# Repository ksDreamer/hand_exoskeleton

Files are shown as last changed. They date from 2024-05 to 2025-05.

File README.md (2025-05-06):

# hand_exoskeleton 低成本机械手外骨骼

[toc]

A low-cost 6DoF hand exoskeleton using linkage and tendon mechanism under ESP32.   

一个约500元低成本6自由度的手部外骨骼，用连杆驱动四指，用线驱模拟肌腱机制驱动大拇指，主控是ESP32，动力源是七个SC09总线舵机，可以承载大于20N的负载。

开源地址：https://github.com/ksDreamer/hand_exoskeleton

视频介绍：[[开源] 500块钱的低成本6自由度手部外骨骼_灵巧手_康复手套](https://www.bilibili.com/video/BV1YzUzY8ETY/)

overview

# News 更新记录

2024-11-16: 完善README，补充细节。DIY电池座的图文攻略已完成。

2024-11-24: 上传3D打印文件，更新README。

2025-05-06: 补充拇指细节

# Getting Started 复现教程

1. 克隆仓库到本地，下载相关资源  ```git clone https://github.com/ksDreamer/hand_exoskeleton.git```

2. 修改机械结构、开始3D打印。机械结构的资源在`mechanics`文件夹里，包含SolidWorks格式模型（零件是`.SLDPRT`，总装是`_概念总装Assembly.SLDASM`，手的模型文件：`Assy 90.SLDPRT`）和FDM的3D打印文件（零件是`.stl`，总装是`_概念总装Assembly.3mf`），需要修改就自行修改（打印手的模型需缩小到原本的0.9）。

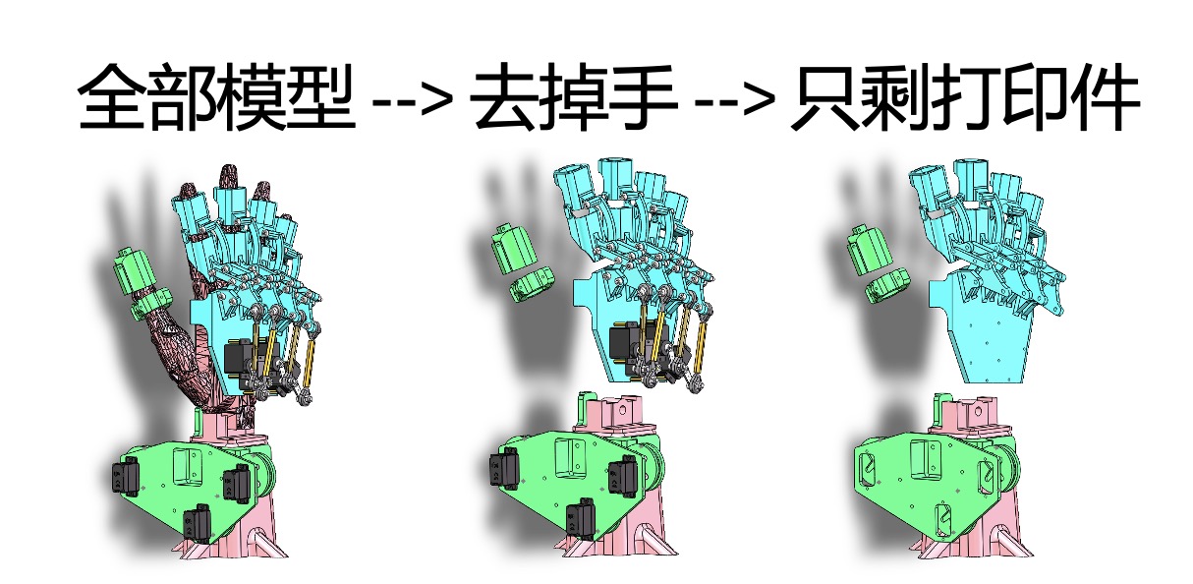
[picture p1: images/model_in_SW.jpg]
model_in_SW
   

   如图，在SOLIDWORKS里找到手的文件后点击隐藏零部件，从而只显示外骨骼。蓝色是四指部分，绿色是大拇指部分，粉色是底座。黑色是舵机，黄色是铜柱，白色是螺丝、鱼眼轴承、舵盘、舵臂。**只有蓝色、绿色和粉色的文件需要3D打印，已全部整理在`mechanics/FDM_3DPrinting`内**。经切片软件处理后3D打印。如果没接触过3D打印，欢迎阅读作者写的教程：[3D 打印机_拓竹 X1Carbon_操作指南](https://zhuanlan.zhihu.com/p/644491008)。建议3D打印时分批次，例如四指的连杆结构尽量安排临近时间打印，拇指的线驱结构也单独打印，避免零件太多混乱。

3. 组装（TODO）。四指的组装相对简单，拇指线驱有一根线要横穿过四指连杆结构的，因为要从这个方向提供拉力。

4. 电控和软件相关资源在`program`文件夹里，需要完整下载ServoDriver文件夹。

5. 配置ESP32的Arduino开发环境：跟着微雪的[Servo Driver with ESP32用户手册](https://www.waveshare.net/w/upload/d/d6/Servo-Driver-with-ESP32-user-manual-cn.pdf)操作。重要的就是选择Board：ESP32 Dev Module。选择串口（不同电脑的串口号不一定相同），注意Mac电脑的串口不叫COM，通常叫usbserial-0001

6. 连上ESP32和舵机后，用Type-C口烧录程序。保持供电。

7. 现在你可以在电脑/手机/平板等智能设备的Wi-Fi列表看到“ESP32_KevinStark"，密码是"88888888"（这些都是你可以自己设置的！），连接后就可以通过局域网访问ESP32的IP地址，从而打开Web前端控制界面了。IP地址通常是`192.168.4.1`。（ESP32支持蓝牙、Wi-Fi、ESP-NOW三种通信方式，ESP-NOW可以做机械手的示教，有空再细写相关内容教程TODO）

8. 设置舵机ID。因为买来新舵机默认ID都是1，所以需要给多个舵机分配不同的ID。通过Web界面的```ID Select+, ID Select-, ID to Set+, ID to Set-```四个按钮，或者手动烧程序来依次设置舵机ID。本项目的ID分配信息如下：大拇指从左往右1、2、3。四指从食指开始为4，小尾指为7。

9. 机械结构安装完成、电控软件准备完毕后，通常来说不能直接运行。因为每个人的安装时的机械调零、铜柱给进量等等可能不一样。建议用串口调试的方法慢慢**测试适合的角度**。

10. 开始玩耍。

# Material 材料

* 机械相关
  * SC09 总线舵机 * 7 
  * 鱼眼轴承 M3 * 8 
  * M2和M3规格的螺丝和螺母若干，六角螺丝刀，十字螺丝刀。
  * 六角铜柱 *4（内径3.2mm，长度20-38mm不定，与鱼眼轴承给进配合和软件角度配合）
  * 线 0.8mm 
  * 3D打印（本项目使用的是PLA耗材和[Bambu Studio](https://bambulab.cn/zh-cn/download/studio)切片软件）
* 电子相关
  * 主控：ESP32 微控制器 * 1 
  * 信号线和串线板（如果采用本项目列出的材料商家，会在每一份舵机包裹里配套这两个）
  * 供电：查询[微雪ESP32的文档](https://www.waveshare.net/wiki/Servo_Driver_with_ESP32)可得知ESP32板的工作电压为6\~12V，接口为5.5*2.1mm DC。查询[微雪SC09 Servo的文档](https://www.waveshare.net/wiki/SC09_Servo)得知SC09舵机的工作电压为4.8\~8.4V。因此我们需要：
    * 支持**6~12V供电**的5521 DC 口电源，因为舵机是串联总线，所以随着舵机数量增多，供电电压要相应增大。
    * 或者2节18650电池（3.7v）**串联** + 5521 DC 转接头 + 电池槽（电池座的制作教程已完成，见下图。注意细节：为了绝缘安全可以加上电工绝缘胶带、热塑管之类的，为了避免多次插拔可以接一个电源开关。但一定要注意安全！没有经验的建议上面那个选项，网购一个适合的适配器电源。）
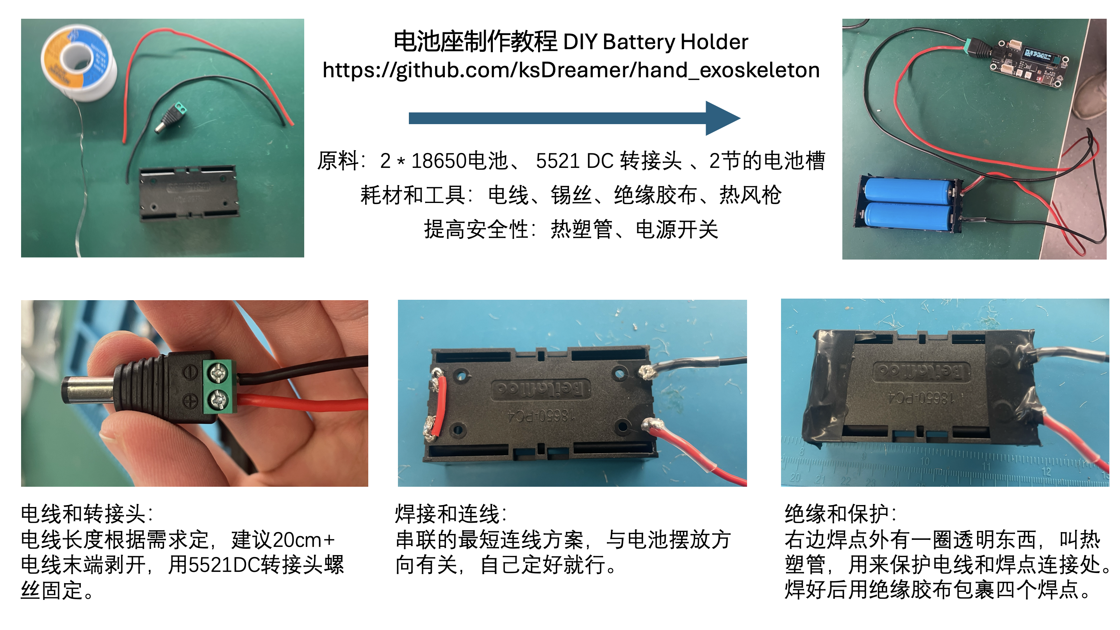
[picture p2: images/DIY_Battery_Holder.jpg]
电池座制作教程
    
  * 电线和锡丝若干
  * 电焊台
  * （可选）热风枪、热塑管、电源开关
* 软件
  * 开发：推荐VSCode开发迭代，Arduino烧录
  * 设备：支持上传程序的电脑，已在Mac和Windows上测试可行。ESP32烧录口是Type-C
  * 使用：任一能连接Wi-Fi且具有图形化窗口的设备

# Mechanics 机械介绍

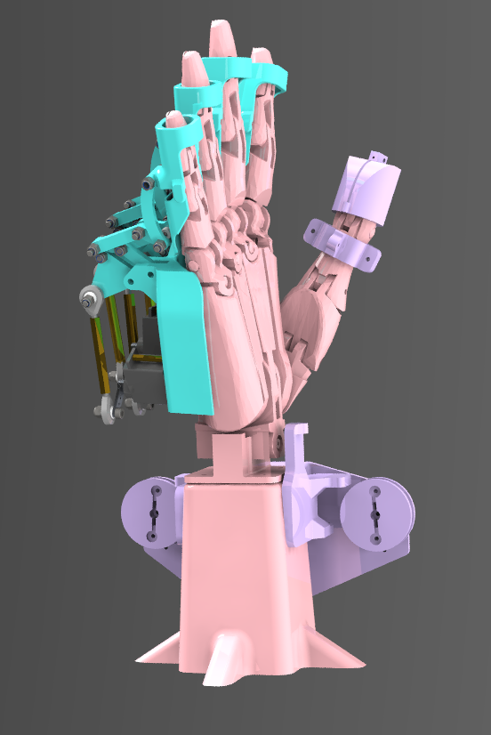
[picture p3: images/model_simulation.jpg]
model_simulation


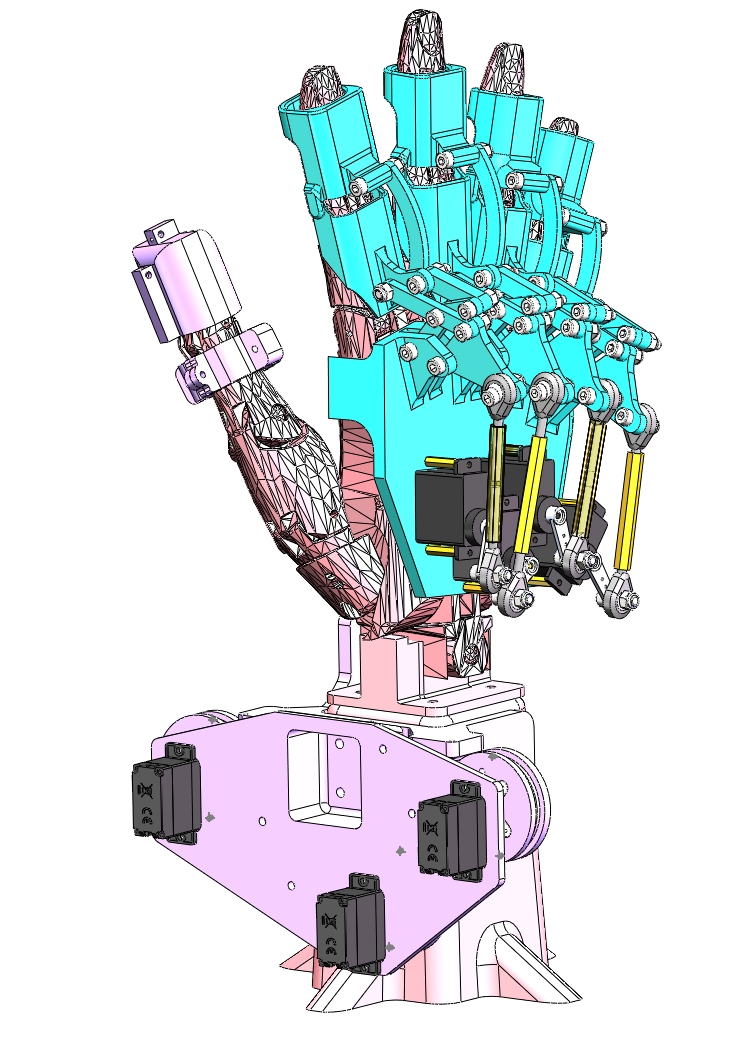
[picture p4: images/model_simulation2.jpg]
model_simulation2


## 基本信息

**连杆**与**线驱**结合控制。

重量：大拇指外骨骼174g，四指外骨骼226g，总重大约400g。（含舵机和各种零件耗材，不含手模型和电源）

尺寸：150x150x310mm

负载：四指总拉力>20N。

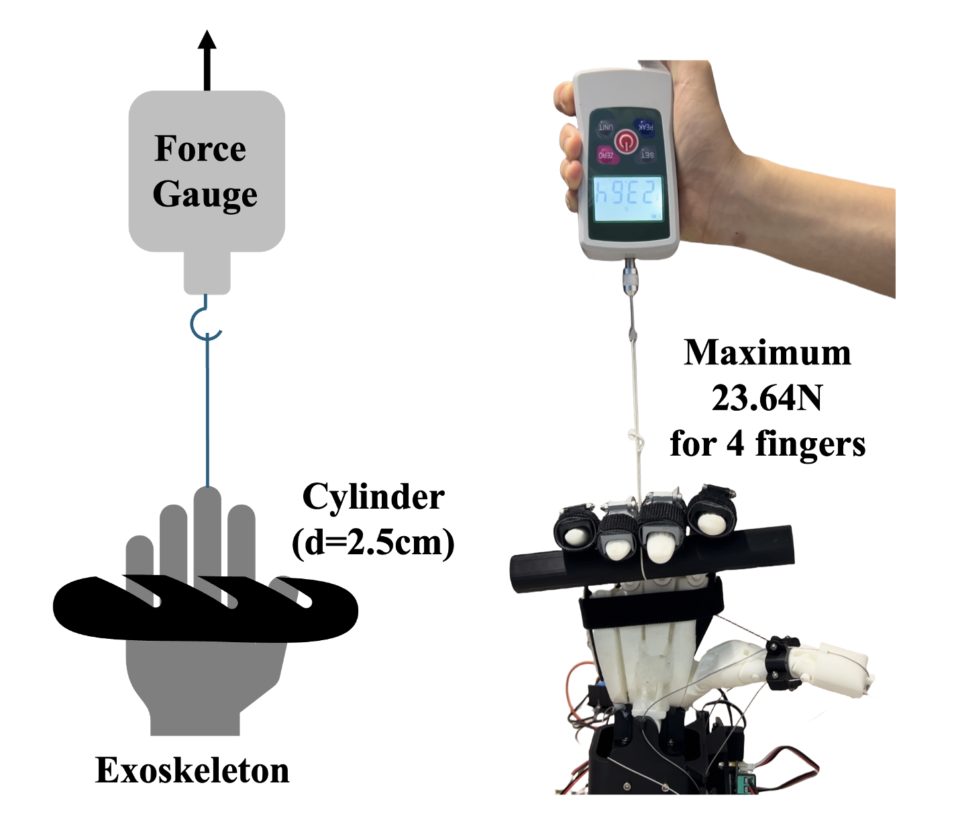
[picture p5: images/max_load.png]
max_load


与手部贴合的部分采用圆角设计，具有良好的舒适性。

四指穿戴方便，直接往手上套。大拇指需要套环和拉线，会复杂一点。

## 四指——连杆

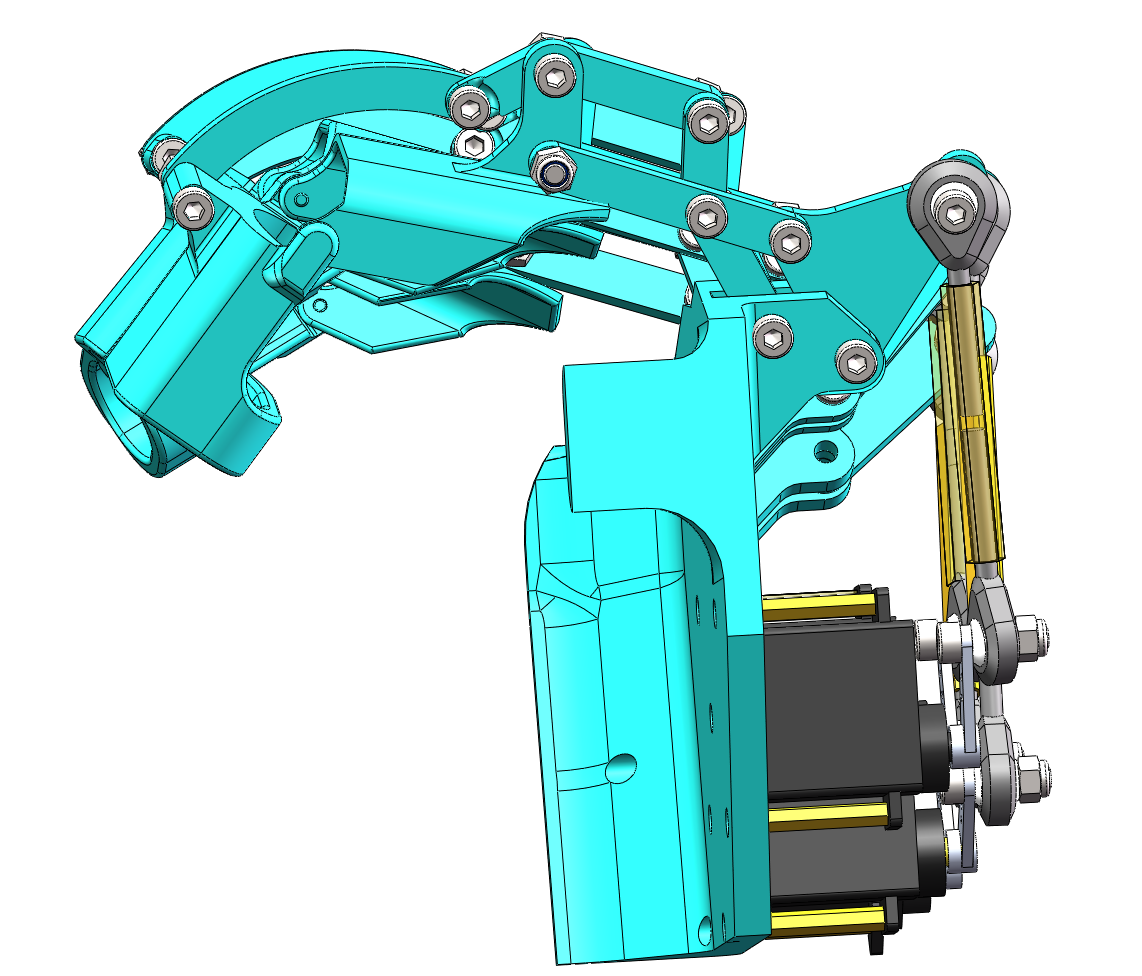
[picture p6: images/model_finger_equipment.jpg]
model_finger_equipment


传动部分通过**曲柄连杆**与**鱼眼轴承**将水平面内的运动转化为手指的竖直运动，并限制摇杆的行程，保证安全性；
执行部分每根手指采用八根连杆的系统控制，考虑到MCP关节两侧没有地方穿戴外骨骼，故通过两个平行四边形四连杆将关节引出，PIP关节通过四连杆设计方式准确控制弯曲程度，并且进一步通过螺丝之间的干涉再次保证手指不会反向弯曲。  

## 大拇指——线驱

大拇指通过三个舵机实现两自由度的紧凑灵活过驱动线驱控制。

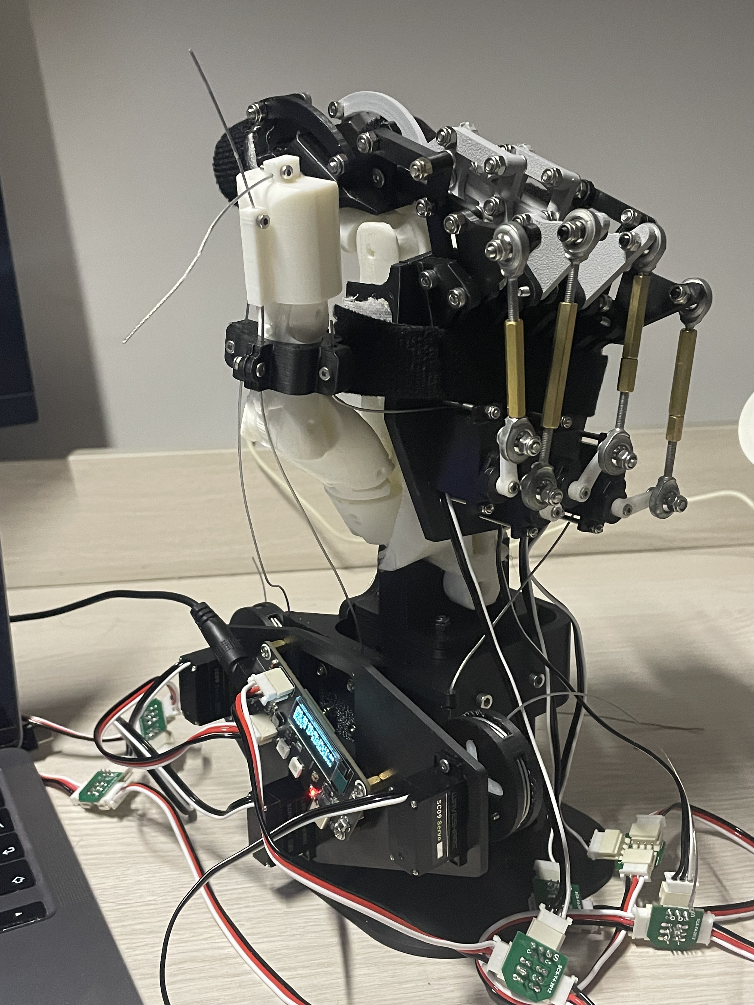
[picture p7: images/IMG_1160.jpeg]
Thumb_1

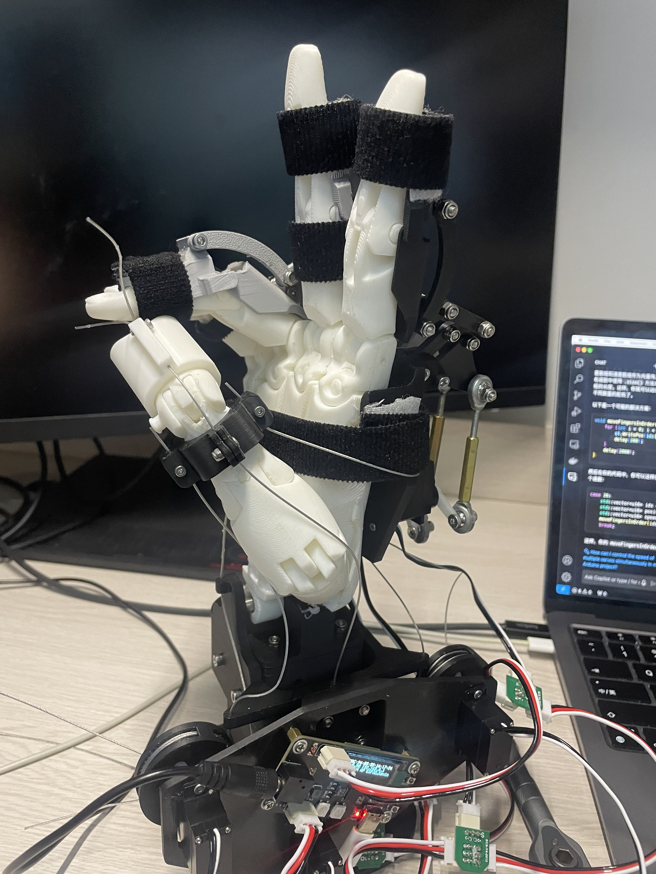
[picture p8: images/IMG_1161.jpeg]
Thumb_2

其中1号舵机和3号舵机控制一个轴的自由度，2号舵机控制水平面垂直另一个轴的自由度。

# Program 程序介绍

## 基本信息

单舵机控制：```st.WritePos(2, 450, 0,400);``` 第一项2表示舵机ID是2，第二项450表示目标角度为450，第四项400表示转动速度为400。第三项不用管。

多舵机同时控制，就把舵机ID、Position和Speed存入相应数组，```st.SyncWritePos(ID, 7, Position, 0, Speed);```分别是舵机ID，舵机数量，角度，第四项不用管，速度。

多舵机控制需要在STSCTRL.h 里定义```byte ID[]、u16 Position[]、u16 Speed[]```，方括号内填数量。

重要参考文档：

* https://www.waveshare.net/wiki/Servo_Driver_with_ESP32 

* https://www.waveshare.net/wiki/SC09_Servo

## ServoDriver.ino

ServoDriver.ino 是主程序，```void loop()```是主函数，在这里写的程序只要主控上电就会自动循环执行。

在 ```void setup()```里这几行的作用是初始化舵机，匹配舵机ID和计算机中的变量

```c++
  ID[0] = 1; //匹配舵机ID，大拇指分别为1,2,3,二到五指为4,5,6,7。有多少个就要在STSCTRL.h的byte ID[]，Position[]，Speed[]里对应修改。
  ID[1] = 2;
  ID[2] = 3;
  ID[3] = 4;
  ID[4] = 5;
  ID[5] = 6;
  ID[6] = 7;
```

只要有供电，就能在Wifi列表找到ESP32的局域网热点。连接后浏览器访问192.168.4.1可以打开web调试界面。（前提是没有把Wi-Fi相关程序注释或删除）

本程序里在```loop```里增加了串口调试的相关程序，方便开发测试。使用方法是：（设置好开发板环境、波特率等之后）Type-C连接电脑和ESP32，在Arduino右上角打开串口监视器。可以有两种输入：

* ```[ID] [Position] [Speed]```格式的单舵机转动命令，需要空格。

* ```[caseNumber]```格式的动作方案。

## CONNECT.h

在这里的```activeCtrl```里面的```switch case```添加想要的动作方案。例如case 23是写好了的```Open Hand```函数。

```c++
case 23: // Open Hand
        openHand();
        moveThumbSameTime(1000, 100, 0, setSpeed);
        break;
```

里面可以直接用前面介绍的```WritePos```等方法直接写你要的转动方案。此处的两个子函数是在外面做了函数定义和封装。查阅CONNECT.h即可查到其定义。

此处就可以做很多动作方案和软件开发相关工作了。如果感兴趣可以直接把微雪官方文件拉下来看看和本项目的有什么区别。

## WEBPAGE.h

WEBPAGE.h 是对Web前端界面的开发。本质是HTML+JavaScript+CSS。  

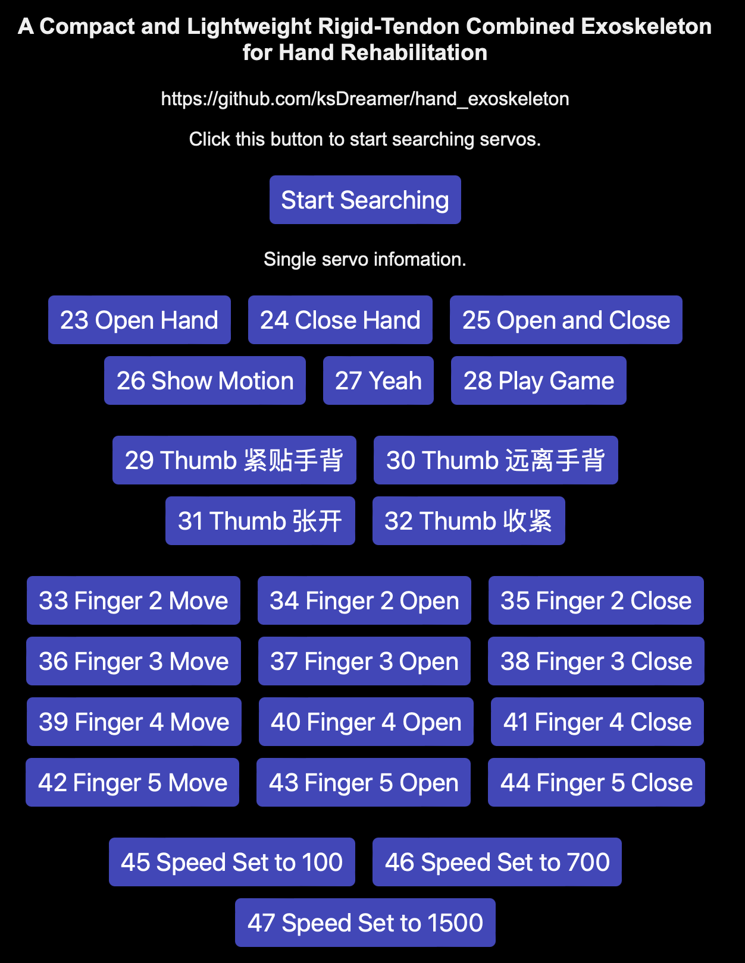
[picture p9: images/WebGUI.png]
WebGUI


要给Web前端开发新功能，想要什么动作方案就在CONNECT.h里的```active Control```函数处添加新case，然后在WEBPAGE.h里调用```toggleCheckbox```函数。（建议从case 30开始，不建议和官方的case重叠覆盖）

例如看下面这个，就是添加了一个叫做“23 Open Hand”的按钮。点击就会触发```toggleCheckbox```函数里的第二个参数对应的case。那case 23是什么呢？就需要你自己去写了，本项目case 23 对应Open Hand

```html
<label align="center"><button class="button" onclick="toggleCheckbox(1, 23, 0, 0);">23 Open Hand</button></label>
```

此处就可以做很多网页前端相关工作了。如果感兴趣可以直接把微雪官方文件拉下来看看和本项目的有什么区别。

## Developing Log 开发日志

* v0.2 测试得到四指和大拇指2号舵机的合适转动角度，放在Loop主函数里。

* v0.3 WEB前端增加四指的Move、Open、Close按钮和动作方案。根据舵臂和装置测试效果重新调整小尾指（7号舵机）转动参数以避免干涉。修改Wifi名为ESP32_KevinStark，密码为88888888。

* v0.4 增加大拇指控制方案，先```relaxThumb```让1和3号舵机的线松驰，再移动；封装了很多函数，增强可维护性；增加了很多动作方案。

* v0.5 优化代码结构，封装函数。大拇指稳定，先张开再收紧。增加动作方案例如四指和大拇指的联动，play game 石头剪刀布。整理Web前端布局。于ServoDriver.ino增加串口调试程序，可接收"[ID] [Position] [Speed]"格式的单舵机转动命令，还有"[caseNumber]"格式的动作方案。

* v1.0 增加三种Speed的选择 100 700 1500 对应case 45 46 47，只改变四指运行速度。简化前端界面。

## Cost 成本

要复现本项目，至少需要这些：

* SC09舵机 单价47元，7个，[微雪 SC09串行总线舵机300度转动角度金属齿轮舵机电机双模式切换](https://detail.tmall.com/item.htm?id=714639378997)

* ESP32开发板 单价80元，1个，[微雪 ESP32舵机驱动扩展板 wifi远程控制 蓝牙通信 支持253个舵机](https://detail.tmall.com/item.htm?id=667483395387)

* 鱼眼轴承 单价1.9元，8个，[气缸鱼眼接头关节轴承向心万向杆端球头SI内丝SA外螺纹连接杆拉杆](https://item.taobao.com/item.htm?id=725305319897)

* 线 单价2.89元，一次10米长，[304不锈钢钢丝绳 晾衣绳遮阳网包塑钢丝绳 细软小包胶钢丝绳 0.8mm](https://detail.tmall.com/item.htm?id=727898238439)

以上共需要427.09元。

电池+焊接一整套大概在30元以内，3D打印大概在30元以内（仅外骨骼最终版 不含手 不含迭代版本，按照0.2元/克PLA价格）

还有机械、电焊的耗材和工具，还有运费。

也就是说，要实现这个项目，在手头有电焊和机械工具的情况下，500元左右能搞定。

## Summary and Future Plan 总结和未来计划

本项目提供了一个低成本的6自由度手部外骨骼方案，四指部分是连杆传动，拇指是线驱。

因为成本的考虑，这个项目成品的运动精度一般，能指定角度，但无法精确。另外也没有力反馈和传感等功能。

这些在各个子领域都有相对成熟的方案了。因此做集成的难度不会很大。（但不是本项目了。舵机和连杆方案在精度和自由度的上限不高，2024-11-16留言）有条件的话，会选择更高精度的驱动方案，例如步进电机、无刷直流等等。

这个项目发展下去，想探索的一个大方向是灵巧手。

* TODO：
  * ~~DIY电池座的图文攻略（已完成）~~
  * ~~整理上传.3mf格式（已完成）~~
  * 整理上传组装细节
  * 用Web前端交互可能会出现点击一次触发3下动作的问题，暂时不清楚为何。是多个事件监视器对上一个窗口？为稳妥，推荐在问题没找到和解决前用串口控制。
* 可发展方向：
  * 主从示教（ESP-NOW通信，机械结构优化减小死区）
  * 摄像头手势识别（match case 已实现，待整理开源。精确随动还要再研究）
  * 人机交互的优化，例如语音识别输入（STT），语音喇叭模块，网页前端美化（CSS），添加用户开机引导步骤等等。
  * 力反馈和柔性接触抓握。
  * 大语言模型做动作规划（LLM+RAG）
  * 强化学习抓握训练。灵巧手抓取泛化性研究。灵巧手数据生成自监督学习研究。

## Acknowledgements 致谢

谢谢[Khlann](https://github.com/Khlann)和[cyatar](https://github.com/cyatar)在嵌入式领域提供建议。

谢谢lvWei指导焊接并分享技巧。

谢谢RobotIC机器人实验室提供了制作过程所需的部分耗材和工具。

手的模型来自助教，如知晓原出处欢迎告知。

# Reference 参考资料

1. Marcin Bonikowski, Mikulás Hajduk, Lucia Koukolova, Wojciech J. Klimasara, Patrycja Mrozek, and Zbigniew Pilat. New trends in the use of robotic devices in motor rehabilitation of upper limbs. In Automation, 2016.
2. Anirban Chowdhury, Shyam Sunder Nishad, Yogesh Kumar Meena, Ashish Dutta, and Girijesh Prasad. Hand-exoskeleton assisted progressive neurorehabilitation using impedance adaptation based challenge level adjustment method. IEEE Transactions on Haptics, 12:128–140, 2019.
3. FeiyunXiao,LiangGu,WenzhangMa,YanheZhu,ZhenZhang,andYongWang.Realtimemotion intention recognition method with limited number of surface electromyography sensors for a 7-dof hand/wrist rehabilitation exoskeleton. Mechatronics, 79:102642, 2021.
4. Phillip Tran, Seokhwan Jeong, Steven L. Wolf, and Jaydev P. Desai. Patient-specific, voice- controlled, robotic flexotendon glove-ii system for spinal cord injury. IEEE Robotics and Automation Letters, 5:898–905, 2020.
5. https://www.waveshare.net/wiki/Servo_Driver_with_ESP32 
6. https://www.waveshare.net/wiki/SC09_Servo

# Contributor 建设者

Mechanics：

CJY, [ZJR](https://github.com/peterstark1900)

Electronics：

[Kevin Stark](https://github.com/ksDreamer), [Khlann](https://github.com/Khlann)

Software:

[Kevin Stark](https://github.com/ksDreamer)

Report and other work:

ZY, LXH, [Kevin Stark](https://github.com/ksDreamer)

Thanks for reading this project. You are welcomed to make contributions to this project. If there is any problem, feel free to raise an issue. Contact me via gmy.kevinstark@gmail.com if needed.

感谢阅读本项目，欢迎复现并提出改进建议。如果有任何问题，随时可以提Issue，有需要的话可以通过 gmy.kevinstark@gmail.com 联系我。

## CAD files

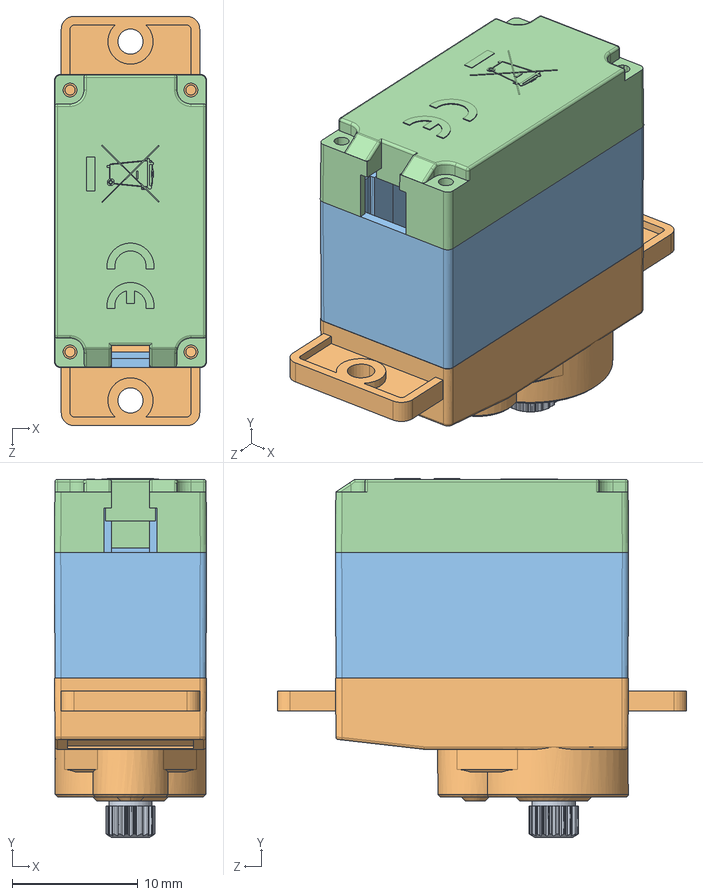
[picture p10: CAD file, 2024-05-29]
mechanics/CAD_SolidWorks/SC09-SERVO.SLDASM
12.1 x 28.5 x 32.5 mm
SJ-CL00-0027-OUTPUTGEAR-0716_37^OUTPUTGEAR_ASM_11_ASM_1_ASM_FT90M-C001_ASM_3_ASM_1_ASM_FT90M-C001-20201118_ASM_1_ASM_SC09-SERVO(2)_SC09-SERVO
SJ-WK00-0038-TOPCASE-0716_41_1^FT90M-C001_ASM_3_ASM_1_ASM_FT90M-C001-20201118_ASM_1_ASM_SC09-SERVO(2)_SC09-SERVO
SJ-WK00-0039-COREMIDDLE-0716_65^FT90M-C001_ASM_3_ASM_1_ASM_FT90M-C001-20201118_ASM_1_ASM_SC09-SERVO(2)_SC09-SERVO
SJ-WK00-0037-BOTTOMCASE-0716_9_^FT90M-C001_ASM_3_ASM_1_ASM_FT90M-C001-20201118_ASM_1_ASM_SC09-SERVO(2)_SC09-SERVO

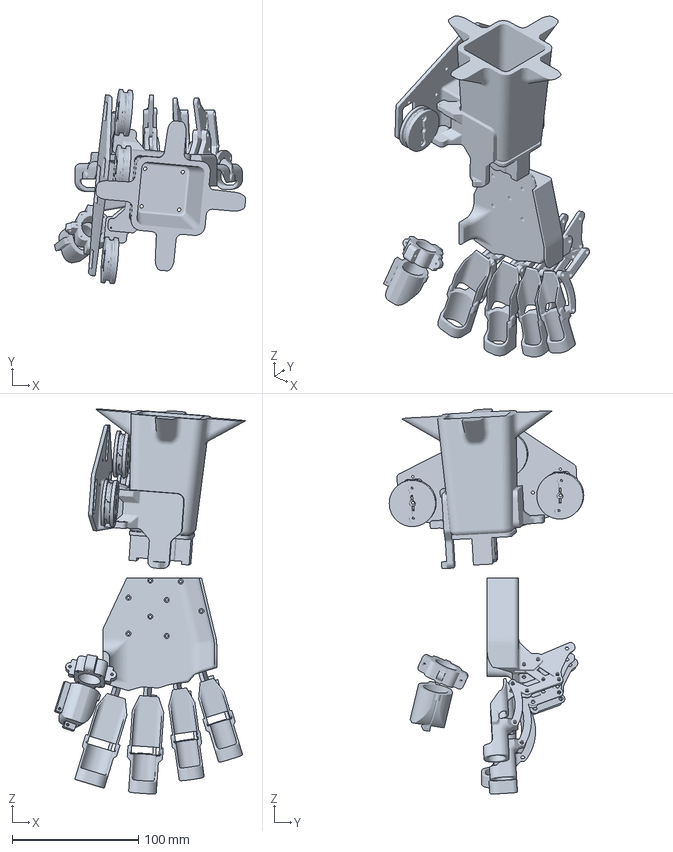
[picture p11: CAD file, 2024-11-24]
mechanics/FDM_3DPrinting/_概念总装Assembly.3MF
151.5 x 154.1 x 304.9 mm

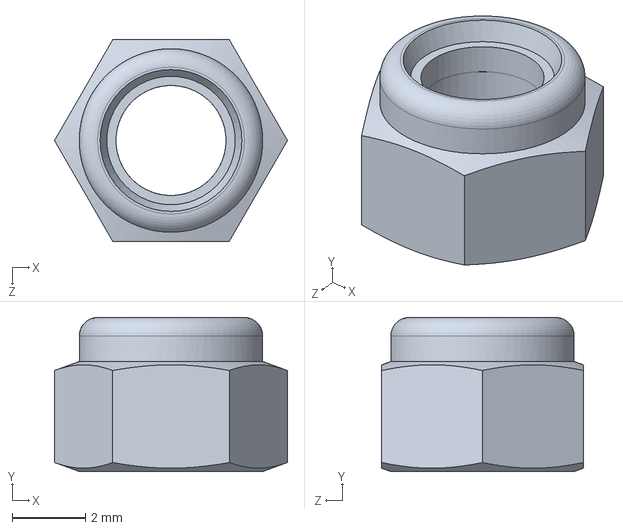
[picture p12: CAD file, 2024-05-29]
mechanics/CAD_SolidWorks/六角防松锁紧螺母.SLDPRT
6.35 x 4.20 x 5.50 mm

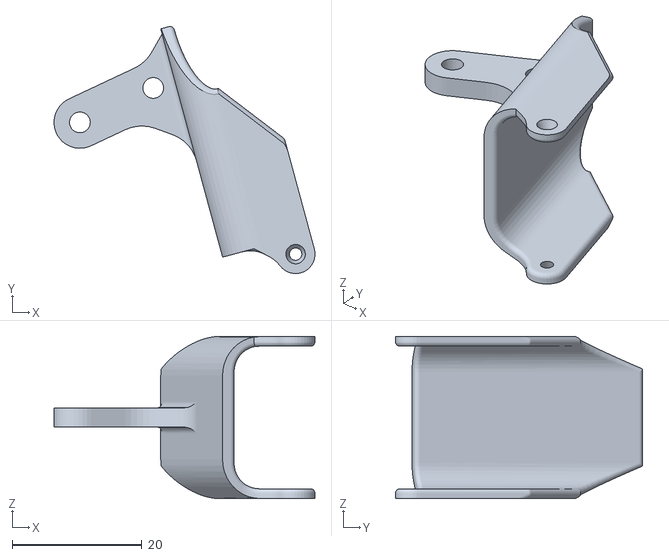
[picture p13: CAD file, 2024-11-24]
mechanics/FDM_3DPrinting/Index食指_2.stl
40.3 x 38.1 x 25.0

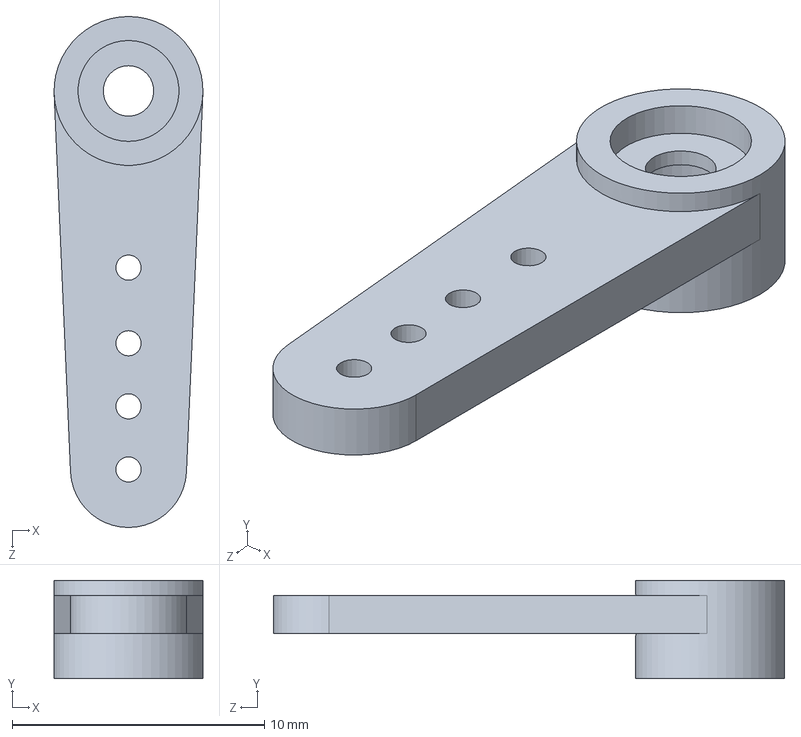
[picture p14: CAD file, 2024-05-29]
mechanics/CAD_SolidWorks/舵臂.SLDPRT
5.90 x 3.90 x 20.2 mm

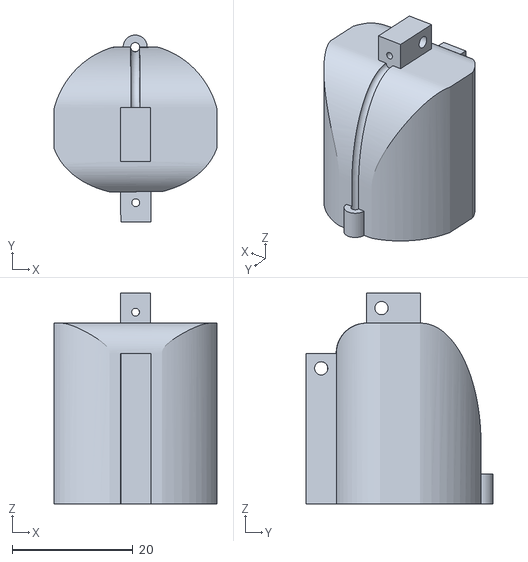
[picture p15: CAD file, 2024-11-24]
mechanics/FDM_3DPrinting/Thumb拇指_末端.stl
27.0 x 31.0 x 35.0

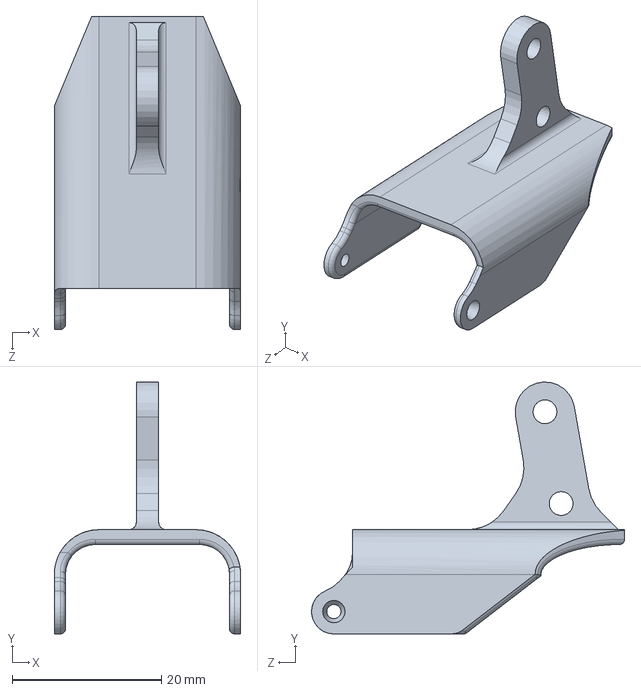
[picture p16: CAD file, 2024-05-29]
mechanics/CAD_SolidWorks/指节一.SLDPRT
25.0 x 33.8 x 42.0 mm

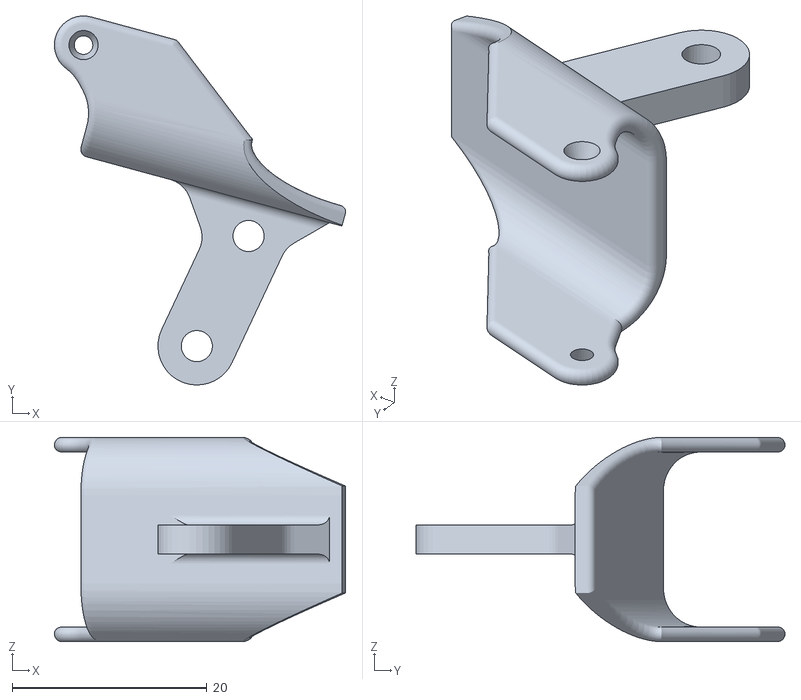
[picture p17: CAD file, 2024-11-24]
mechanics/FDM_3DPrinting/Little小指_2.stl
29.9 x 37.9 x 21.0

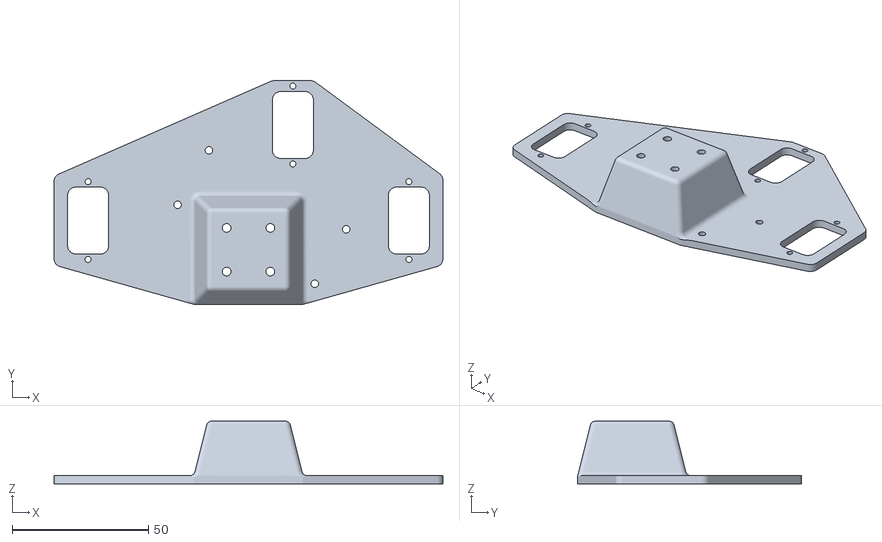
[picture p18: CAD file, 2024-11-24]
mechanics/FDM_3DPrinting/底座_拇指三个舵机的固定架.stl
142.5 x 82.0 x 23.0

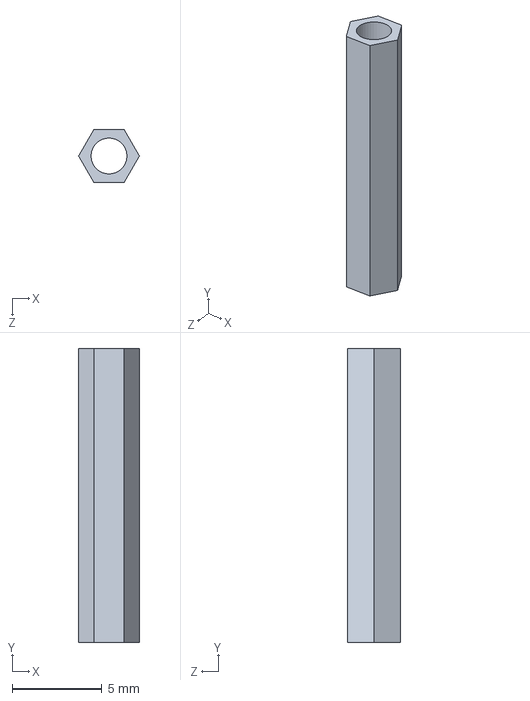
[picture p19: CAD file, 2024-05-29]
mechanics/CAD_SolidWorks/机械手概念铜柱.SLDPRT
3.39 x 16.4 x 2.94 mm

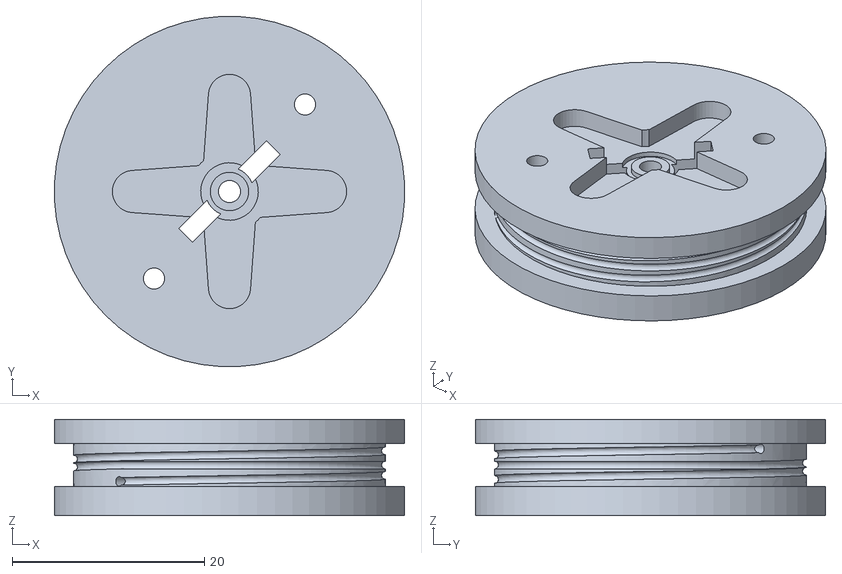
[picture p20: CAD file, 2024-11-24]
mechanics/FDM_3DPrinting/舵盘_2.stl
36.4 x 36.4 x 10.0

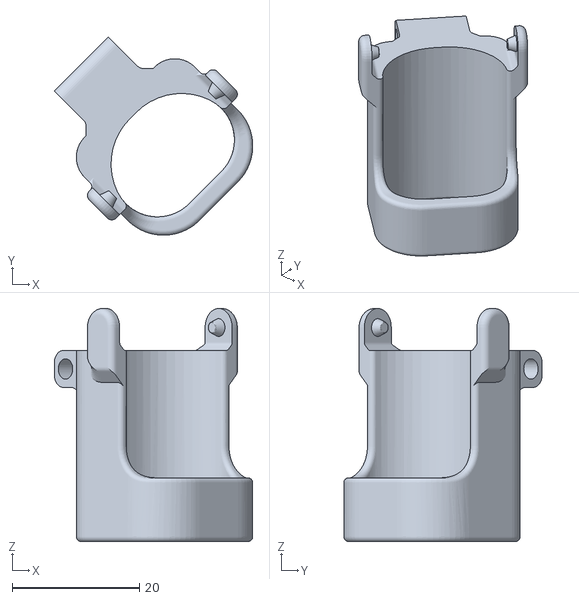
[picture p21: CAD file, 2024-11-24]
mechanics/FDM_3DPrinting/Index食指_1.stl
31.2 x 31.2 x 36.6

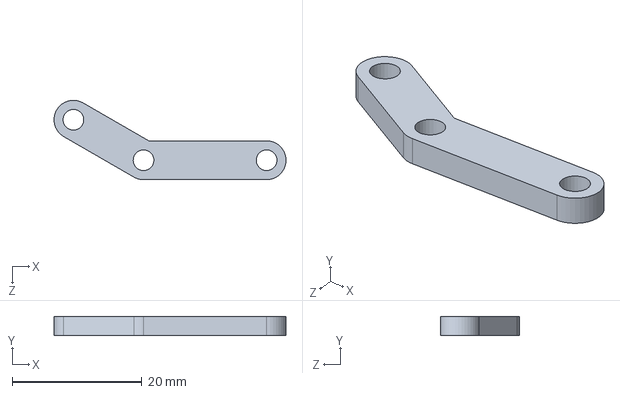
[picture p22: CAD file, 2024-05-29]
mechanics/CAD_SolidWorks/FGH.SLDPRT
35.8 x 3.00 x 12.2 mm

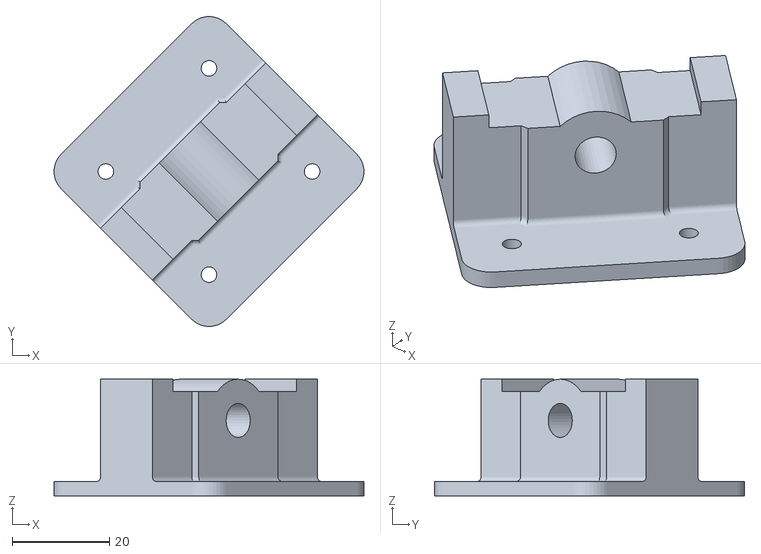
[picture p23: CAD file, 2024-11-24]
mechanics/FDM_3DPrinting/底座_手腕.stl
63.7 x 63.7 x 24.0

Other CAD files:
mechanics/CAD_SolidWorks/Thumb-tip-0428.SLDPRT
mechanics/CAD_SolidWorks/truntable-thumb-big-0406.SLDPRT
mechanics/CAD_SolidWorks/内六角圆柱头螺钉.SLDPRT
mechanics/FDM_3DPrinting/四指连杆_曲_4.stl
mechanics/CAD_SolidWorks/DE.SLDPRT
mechanics/CAD_SolidWorks/EGI.SLDPRT
mechanics/CAD_SolidWorks/HJK.SLDPRT
mechanics/CAD_SolidWorks/MK.SLDPRT
mechanics/CAD_SolidWorks/SC09十字舵盘.SLDPRT
mechanics/CAD_SolidWorks/Thumb-MP-IP-0428-v2.SLDPRT
mechanics/CAD_SolidWorks/arm_wrist-0426.SLDPRT
mechanics/CAD_SolidWorks/servo-sc09.SLDPRT
mechanics/CAD_SolidWorks/servo-support-0411.SLDPRT
mechanics/CAD_SolidWorks/手环.SLDPRT
mechanics/CAD_SolidWorks/手背.SLDPRT
mechanics/CAD_SolidWorks/手臂.SLDPRT
mechanics/CAD_SolidWorks/指节二.SLDPRT
mechanics/CAD_SolidWorks/草图.SLDPRT
mechanics/CAD_SolidWorks/铜柱m3.SLDPRT
mechanics/CAD_SolidWorks/鱼眼轴承m3.SLDPRT
mechanics/CAD_SolidWorks/鱼眼轴承球.SLDPRT
mechanics/FDM_3DPrinting/Little小指_1.stl
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

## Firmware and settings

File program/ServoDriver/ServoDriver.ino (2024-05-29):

// A Compact and Lightweight Rigid-Tendon Combined Exoskeleton for Hand Rehabilitation
// Author: Kevin Stark
// Open Source: https://github.com/ksDreamer/hand_exoskeleton

// ServoDriver.ino 是主程序，void loop()是主函数，在这里写的驱动舵机转动的程序上电会自动循环执行。
// 单舵机控制：st.WritePos(2, 450, 0,400); 分别是ID，角度，未知填0即可，速度。
// 多舵机同时控制，就把舵机ID、Position和Speed存入相应数组，用st.SyncWritePos(ID, 7, Position, 0, Speed);分别是舵机ID，舵机数量，角度，未知填0即可，速度。
// 多舵机控制需要在STSCTRL.h 里定义byte ID[]、u16 Position[]、u16 Speed[]，方括号填数量。
// 如果整个ServoDriver程序包正确烧录到ESP32，只要有供电，就能在Wifi列表找到开发板的局域网热点。连接后浏览器访问192.168.4.1可以打开web调试界面。
// WEBPAGE.h 是对web前端界面的开发。例如可以在里面找到Open Hand 和Close Hand两个函数，分别对应四指的平展和弯曲。
// 要给web前端开发新功能，请在WEBPAGE.h找到toggleCheckbox函数，会发现四个参数，第二个就是case，想要什么动作方案就在CONNECT.h里的active Control函数处添加新case（建议从case 30开始），然后在WEBPAGE.h里调用toggleCheckbox函数。
// 项目重要参考资料：https://www.waveshare.net/wiki/Servo_Driver_with_ESP32 和 https://www.waveshare.net/wiki/SC09_Servo

// 开发日志Developing Log：
// v0.2 测试得到四指和大拇指2号舵机的合适转动角度，放在Loop主函数里。
// v0.3 WEB前端增加四指的Move、Open、Close按钮和动作方案。根据舵臂和装置测试效果重新调整小尾指（7号舵机）转动参数以避免干涉。修改Wifi名为ESP32_KevinStark，密码为88888888。
// v0.4 增加大拇指控制方案，先relaxThumb让1和3号舵机的线松驰，再移动；封装了很多函数，增强可维护性；增加了很多动作方案。
// v0.5 优化代码结构，封装函数。大拇指稳定，先张开再收紧。增加动作方案例如四指和大拇指的联动，play game 石头剪刀布。整理Web前端布局。于ServoDriver.ino增加串口调试程序，可接收"[ID] [Position] [Speed]"格式的单舵机转动命令，还有"[caseNumber]"格式的动作方案。
// v1.0 增加三种Speed的选择 100 700 1500 对应case 45 46 47，只改变四指运行速度。简化前端界面。

// WIFI_AP settings.
const char* AP_SSID = "ESP32_KevinStark";
const char* AP_PWD  = "88888888";

// WIFI_STA settings.
const char* STA_SSID = "OnePlus 8";
const char* STA_PWD  = "40963840";

// the MAC address of the device you want to ctrl.
uint8_t broadcastAddress[] = {0x08, 0x3A, 0xF2, 0x93, 0x5F, 0xA8};
// uint8_t broadcastAddress[] = {0xFF, 0xFF, 0xFF, 0xFF, 0xFF, 0xFF};


typedef struct struct_message {
  int ID_send;
  int POS_send;
  int Spd_send;
} struct_message;

// Create a struct_message called myData
struct_message myData;

// set the default role here.
// 0 as normal mode.
// 1 as leader, ctrl other device via ESP-NOW.
// 2 as follower, can be controled via ESP-NOW.
#define DEFAULT_ROLE 0

// set the default wifi mode here.
// 1 as [AP] mode, it will not connect other wifi.
// 2 as [STA] mode, it will connect to know wifi.
#define DEFAULT_WIFI_MODE 1

// the uart used to control servos.
// GPIO 18 - S_RXD, GPIO 19 - S_TXD, as default.
#define S_RXD 18
#define S_TXD 19

// the IIC used to control OLED screen.
// GPIO 21 - S_SDA, GPIO 22 - S_SCL, as default.
#define S_SCL 22
#define S_SDA 21

// the GPIO used to control RGB LEDs.
// GPIO 23, as default.
#define RGB_LED   23
#define NUMPIXELS 10

// set the max ID.
int MAX_ID = 20;

// modeSelected.
// set the SERIAL_FORWARDING as true to control the servos with USB.
bool SERIAL_FORWARDING = false;

// OLED Screen Dispaly.
// Row1: MAC address.
// Row2: VCC --- IP address.
// Row3: MODE:Leader/Follower  [AP]/[STA][RSSI]
//       DEFAULT_ROLE: 1-Leader(L)/ 2-Follower(F).
//       DEFAULT_WIFI_MODE: 1-[AP]/ 2-[STA][RSSI] / 3-[TRY:SSID].
//       (no matter what wifi mode you select, you can always ctrl it via ESP-NOW.)
// Row4: the position of servo 1, 2 and 3.
String MAC_ADDRESS;
IPAddress IP_ADDRESS;
byte   SERVO_NUMBER;
byte   DEV_ROLE;
byte   WIFI_MODE;
int    WIFI_RSSI;




// set the interval of the threading.
#define threadingInterval 600
#define clientInterval    10

#if CONFIG_FREERTOS_UNICORE
#define ARDUINO_RUNNING_CORE 0
#else
#define ARDUINO_RUNNING_CORE 1
#endif

#include "RGB_CTRL.h"
#include "STSCTRL.h"
#include "CONNECT.h"
#include "BOARD_DEV.h"



void setup() {
  Serial.begin(115200);
  while(!Serial) {}

  espNowInit();

  getMAC();
  
  boardDevInit();

  RGBcolor(0, 64, 255);

  servoInit();

  wifiInit();

  webServerSetup();

  RGBoff();

  ID[0] = 1; //匹配舵机ID，大拇指分别为1,2,3,二到五指为4,5,6,7。有多少个就要在STSCTRL.h的byte ID[]，Position[]，Speed[]里对应修改。
  ID[1] = 2;
  ID[2] = 3;
  ID[3] = 4;
  ID[4] = 5;
  ID[5] = 6;
  ID[6] = 7;

  delay(1000);
  pingAll(true);

  threadInit();
}


void loop() {
//  delay(300000);

// 四指串口输入的语法: ID[空格]Position[空格]ID[空格]Position[空格]...[空格]Speed;
    if (Serial.available() > 0) { // 检查是否有可用的数据
        int firstNumber = Serial.parseInt(); // 读取第一个数字

        if (Serial.peek() == ' ') { // 检查下一个字符是否是空格
            // 如果是空格，那么读取后面的数字并控制舵机
            Serial.read(); // 跳过空格
            int ID = firstNumber;
            int Position = Serial.parseInt(); // 读取舵机的角度
            if (Serial.read() == ' ') { // 跳过空格
                int Speed = Serial.parseInt(); // 读取舵机的速度
                st.WritePos(ID, Position, 0, Speed); // 控制舵机
                Serial.write("Servo ");
                Serial.print(ID);
                Serial.write(" moves to Position ");
                Serial.print(Position);
                Serial.write(" with Speed ");
                Serial.println(Speed);
                delay(7000);
            }
        }
        else {
            // 如果只输入单个数字，没有空格，那么根据第一个数字执行相应的 case
            activeCtrl(firstNumber);
            }
    }
}


// 舵机顺时针转，角度由小变大。四号和五号舵机在舵机左边旋转，所以其变化与在舵机右边旋转的六号和七号舵机相反。
// 舵臂拉到远端是平，所以平的时候4、5号舵机是小角度，6、7号舵机是大角度。曲的时候4、5号舵机是大角度，6、7号舵机是小角度。

// activeCtrl(25); // Open and Close four fingers one by one, ID order: 4,5,6,7,4,5,6,7
// activeCtrl(26); // Open and Close four fingers one by one, ID order: 4,5,6,7,7,6,5,4
// activeCtrl(27); // 'Yeah', Simulatously Open ID 4 and 5, Close ID 6 and 7.
// activeCtrl(30); // 四指张开
// activeCtrl(31); // 四指合拢

// 官方示例代码
//   st.WritePosEx(1, 0, 600, 0);
//   delay(3000);
//   st.WritePosEx(1, 180, 600, 0);
  // st.WritePosEx(3, 25, 600, 0);
  // delay(2000);

  // st.WritePosEx(1, 1000, 600, 0);
  // st.WritePosEx(2, 1000, 600, 0);
  // st.WritePosEx(3, 1000, 600, 0);
  // delay(2000);
  
// > > > > > > > > > DOC < < < < < < < < <
// === Develop Board Ctrl ===
// get the MAC address and save it in MAC_ADDRESS;
// getMAC();

// Init GPIO.
// pinMode(PIN_NUM, OUTPUT);
// pinMode(PIN_NUM, INPUT_PULLUP);

// set the level of GPIO.
// digitalWrite(PIN_NUM, LOW);
// digitalWrite(PIN_NUM, HIGH);

// PWM output(GPIO).
// int freq = 50;
// resolution = 12;
// ledcSetup(PWM_NUM, frep, resolution);
// ledcAttachPin(PIN_NUM, PWM_NUM);
// ledcWrite(PWM_NUM, PWM);


// === Servo Ctrl ===
// GPIO 18 as RX, GPIO 19 as TX, init the serial and the servos.
// servoInit();

// set the position as middle pos.
// setMiddle(servoID);
// st.WritePosEx(ID, position, speed, acc);



// === Devices Ctrl ===
// ctrl the RGB.
// 0 < (R, G, B) <= 255
// setSingleLED(LED_ID, matrix.Color(R, G, B));

// init the OLED screen, RGB_LED.
// boardDevInit();

// dispaly the newest information on the screen.
// screenUpdate();

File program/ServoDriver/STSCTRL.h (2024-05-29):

#include <SCServo.h>
#include <math.h>
//
byte ID[7]; //关于舵机ID的设置，请参考https://www.waveshare.net/wiki/SC09_Servo里的“更改舵机ID”。
u16 Position[7];
u16 Speed[7];


// === SC Servo ===
#define CTRL_SC_SERVO
SCSCL st;
float ServoDigitalRange = 1023.0;
float ServoAngleRange   = 210.0;
float ServoDigitalMiddle= 511.0;
#define ServoInitACC      0
#define ServoMaxSpeed     1500
#define MaxSpeed_X        1500
#define ServoInitSpeed    1500
int SERVO_TYPE_SELECT = 2;
int MAX_MIN_OFFSET = 30;
#define SMS_STS_ID SCSCL_ID

// === ST Servo ===
// #define CTRL_ST_SERVO
// SMS_STS st;
// float ServoDigitalRange = 4095.0;
// float ServoAngleRange   = 360.0;
// float ServoDigitalMiddle= 2047.0;
// #define ServoInitACC      100
// #define ServoMaxSpeed     4000
// #define MaxSpeed_X        4000
// #define ServoInitSpeed    2000
// int SERVO_TYPE_SELECT = 1

// set the servo ID list.
byte ID_List[253];
bool Torque_List[253];

// []: the ID of the servo.
// the buffer of the information read from the active servo.
s16  loadRead[253];
s16  speedRead[253];
byte voltageRead[253];
int  currentRead[253];
s16  posRead[253];
s16  modeRead[253];
s16  temperRead[253];

// []: the num of the active servo.
// use listID[activeNumInList] to get the ID of the active servo.
byte listID[253];
byte searchNum = 0;
bool searchedStatus = false;
bool searchFinished = false;
bool searchCmd      = false;
byte activeNumInList = 0;
s16 activeServoSpeed = 100;
byte servotoSet = 0;

// linkageBuffer to save the angle.
float linkageBuffer[50];

// the buffer of the bytes read from USB-C and servos. 
int usbRead;
int stsRead;


void getFeedBack(byte servoID){
  if(st.FeedBack(servoID)!=-1){
    posRead[servoID] = st.ReadPos(-1) ; // For bigger servo, eg SC 15. If leader and follower are the same, then delete '* 1.67'.
    speedRead[servoID] = st.ReadSpeed(-1);
    loadRead[servoID] = st.ReadLoad(-1);
    voltageRead[servoID] = st.ReadVoltage(-1);
    currentRead[servoID] = st.ReadCurrent(-1);
    temperRead[servoID] = st.ReadTemper(-1);
    modeRead[servoID] = st.ReadMode(servoID);
  }else{
    // Serial.println("FeedBack err");
  }
}


void servoInit(){
  Serial1.begin(1000000, SERIAL_8N1, S_RXD, S_TXD);
  st.pSerial = &Serial1;
  while(!Serial1) {}

  for (int i = 0; i < MAX_ID; i++){
    Torque_List[i] = true;
  }
}


void setMiddle(byte InputID){
  st.CalibrationOfs(InputID);
}


void setMode(byte InputID, byte InputMode){
  st.unLockEprom(InputID);
  if(InputMode == 0){
    if(SERVO_TYPE_SELECT == 1){
      st.writeWord(InputID, 11, 4095);
      st.writeByte(InputID, SMS_STS_MODE, InputMode);
    }
    else if(SERVO_TYPE_SELECT == 2){
      st.writeWord(InputID, SCSCL_MIN_ANGLE_LIMIT_L, 20);
      // st.writeWord(InputID, SCSCL_MIN_ANGLE_LIMIT_H, 5123);
      st.writeWord(InputID, SCSCL_MAX_ANGLE_LIMIT_L, 1003);
      // st.writeWord(InputID, SCSCL_MAX_ANGLE_LIMIT_H, 60240);
    }
  }

  else if(InputMode == 3){
    if(SERVO_TYPE_SELECT == 1){
      st.writeByte(InputID, SMS_STS_MODE, InputMode);
      st.writeWord(InputID, 11, 0);
    }
    else if(SERVO_TYPE_SELECT == 2){
      st.writeWord(InputID, SCSCL_MIN_ANGLE_LIMIT_L, 0);
      // st.writeWord(InputID, SCSCL_MIN_ANGLE_LIMIT_H, 0);
      st.writeWord(InputID, SCSCL_MAX_ANGLE_LIMIT_L, 0);
      // st.writeWord(InputID, SCSCL_MAX_ANGLE_LIMIT_H, 0);
    }
  }
  st.LockEprom(InputID);
}


void setID(byte ID_select, byte ID_set){
  if(ID_set > MAX_ID){MAX_ID = ID_set;}
  st.unLockEprom(ID_select);
  st.writeByte(ID_select, SMS_STS_ID, ID_set);
  st.LockEprom(ID_set);
}


void servoStop(byte servoID){
  st.EnableTorque(servoID, 0);
  delay(10);
  st.EnableTorque(servoID, 1);
}


void servoTorque(byte servoID, u8 enableCMD){
  st.EnableTorque(servoID, enableCMD);
}

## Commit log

2024-05-29 add mechanics and program
    [DE.SLDPRT, EGI.SLDPRT, FGH.SLDPRT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]
2024-05-29 updates README.md, more details. Uncommented some ID setting buttons in WEBPAGE.h for users to set servo ID
2024-11-16 2024-11-16: 完善README，补充细节。DIY电池座的图文攻略已完成。
2024-11-17 update the voltage description in REAMDE
2024-11-24 add 3DPrinting files, update README
    [DE.SLDPRT, EGI.SLDPRT, FGH.SLDPRT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]
